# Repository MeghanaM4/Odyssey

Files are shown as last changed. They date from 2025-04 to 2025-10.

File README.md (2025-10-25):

# Odyssey

> a project for [apex.hackclub.com](https://apex.hackclub.com) by Meghana Madiraju and help from Kieran Klukas

I have been in love with space for as long as I can remember, so when I heard Hack Club was letting teenagers send whatever they want 113,000 feet in the air I knew I had to do it. We get $100 per person to make an invention that'll go onto a high altitude balloon (HAB), and if you spend 30 hours on it you'll get to go to Boston for a hackathon where everyone will launch their payloads at the same time and make cool stuff.

## Quick Overview (what we're sending up)
- Sensor data from SMD components on PCB (stored on a microSD card)
- PCB powered by 3 AA batteries that can survive -45C
- Internal camera that can see internal content
- 8 digit 7-segment display that show the current altitude, which the int. camera can also see

## Collected data
- Pressure
- Magnetic field (3-axis)
- Internal temperature of payload
- Gyroscopic data (3-axis)

## Component Stack
| Component | Purpose |
| --- | --- |
| Seeed Studio XIAO RP2040 | Main microcontroller |
| MS560702BA03-50 | Altimeter |
| MPU-6050 | Gyroscope/accelerometer |
| ALS31313KLEATR-1000 | Magnetometer |
| Mini Body Cam | Internal view of payload | 

View the complete BOM [here](https://docs.google.com/spreadsheets/d/1y77u3fouo9j1fYMRJqijLE8DN1v_GkXtAQhd4oCJCtc/edit?usp=sharing)          
<br>
## PCB
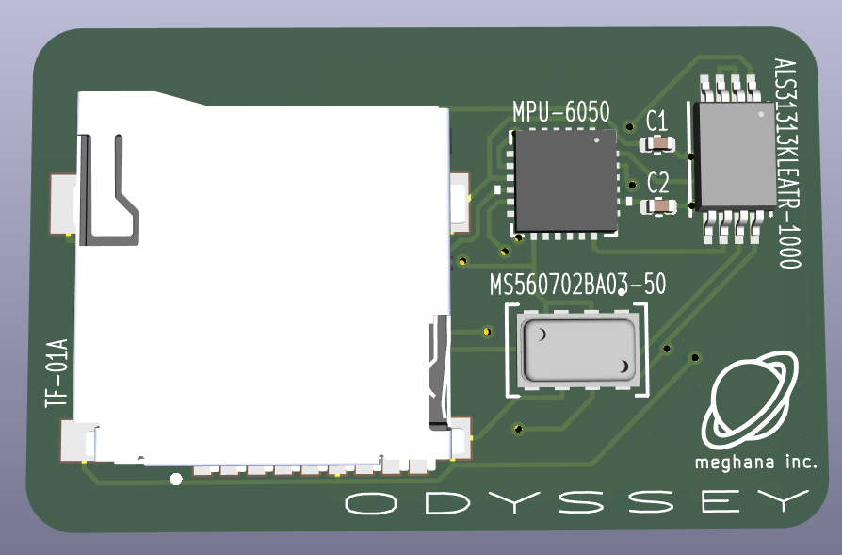
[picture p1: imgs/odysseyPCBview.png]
Odyssey PCB CAD rendering
             
<br>

## Timeline
| Phase | Status (%)|
| --- | --- |
| Research + Planning | 100% |
| Designing PCB and electronics layout | 100% | 
| Building payload | 100% |
| Coding firmware | 100% |
| Final tests and edits | 100% |
| Launch | 100% |

## Internal Camera View
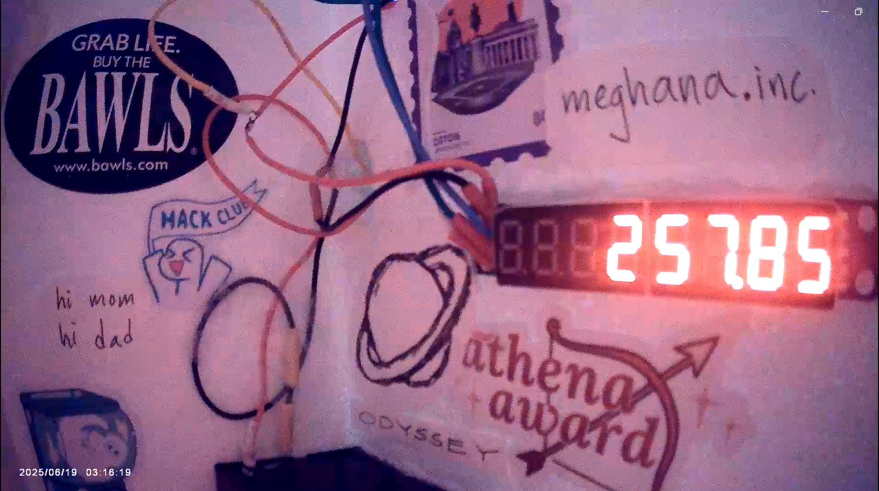
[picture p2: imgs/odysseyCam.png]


## External View


## Design Process
My first sketch of Odyssey looked like this:
<br>
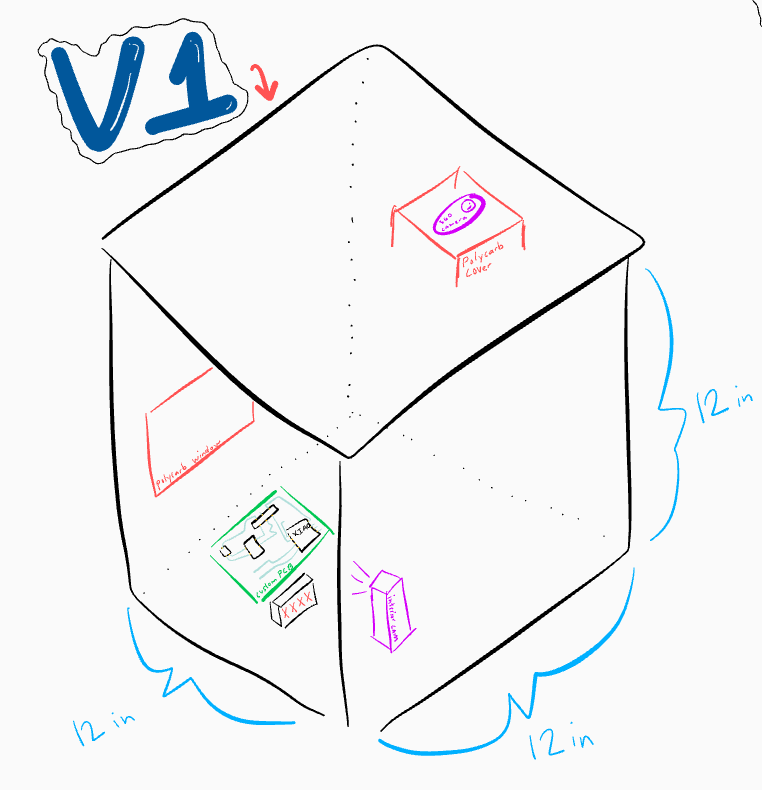
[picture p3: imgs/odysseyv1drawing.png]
Odyssey v1 drawing

<br>
The main PCB (the green square artfully drawn in the center, complete with blue copper traces) with the XIAO and SMDs would process and collect data. The 4 digit 7-segment display displays the altitude of the payload (math that would be calculated from the barometer), and would sit in front of an internal camera (the purple box) so the altitude could be captured in the video feed. The internal camera would also look outside via the polycarbonate window that I am going to steal from my robotics team's shop (sorry Mr. S).      
The camera on top was originally meant to capture the sky, but then I found out all the payloads would be aligned on top of eachother candy-necklace style, so I scrapped that pretty quick.

The second sketch had some improvements:
<br>
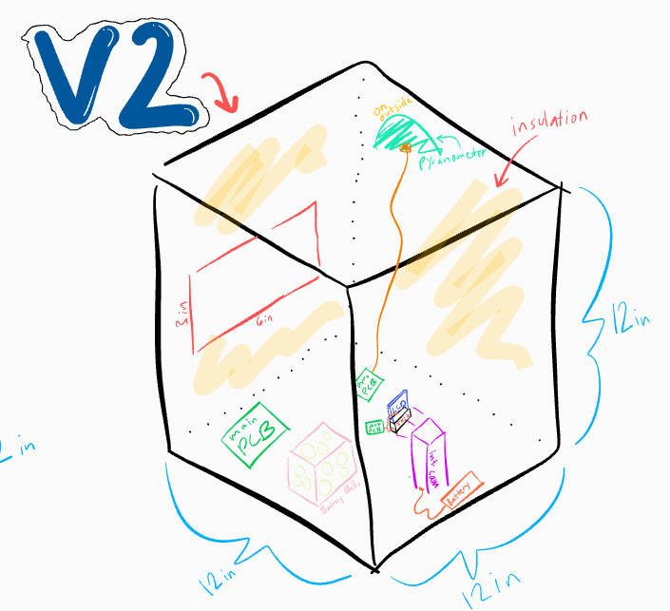
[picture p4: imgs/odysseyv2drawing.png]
Odyssey v2 drawing

<br>

I thought that we would need 3 PCBs: one for the main sensors, one for the LCD screen and 7-seg display, and one for the pyranometer. What's overkill? This obviously was taken out after I thought about a bit more (see: overkill) and after I saw the customs and duties taxes. The yellow stuff you see on the walls is my artistic interpretation of spray insulation.      

I really wanted our data to be space-focused, so getting a pyranometer to measure cosmic ray data was at the top of my list. Unfortunately, the Apogee Instrument component I found was a massive pain to work with, so I decided to just scrap it. If I get the basic functionality of everything else working, then I'll look into aurora borealis or radiation detection. The challenge is that those have to be on the outside of the payload, or at least shielded solely by polycarb or some other low-z window material.

I also drew a sketch of what I wanted the internal view to be:
<br>
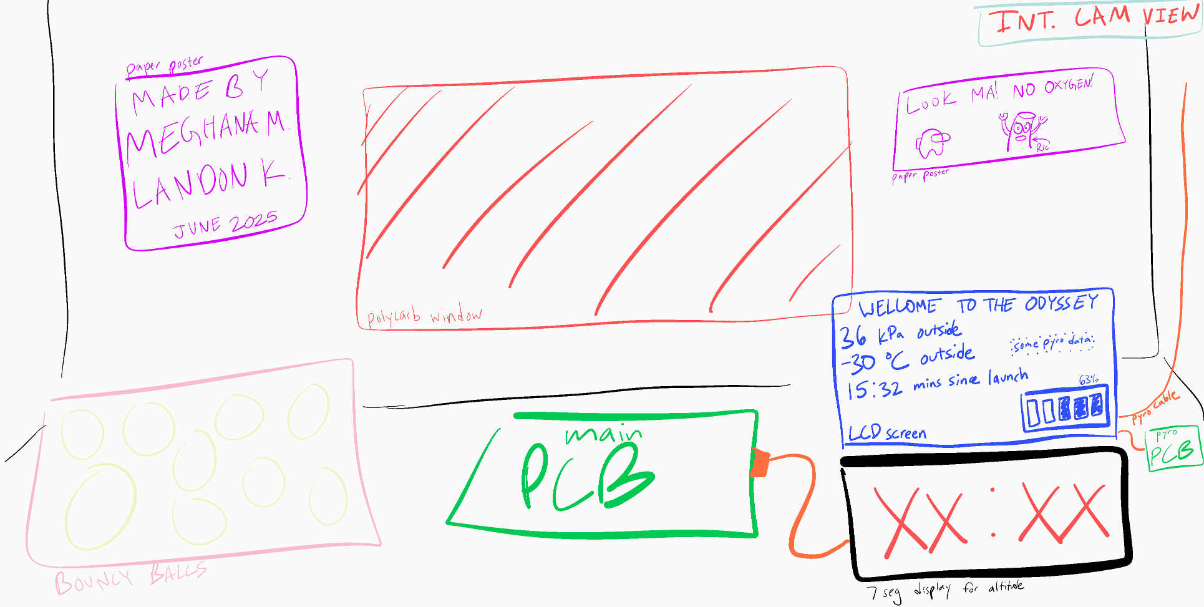
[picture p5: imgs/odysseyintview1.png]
Odyssey internal camera view v1

<br>

Here's an updated internal view with a smaller box and an updated layout:
<br>
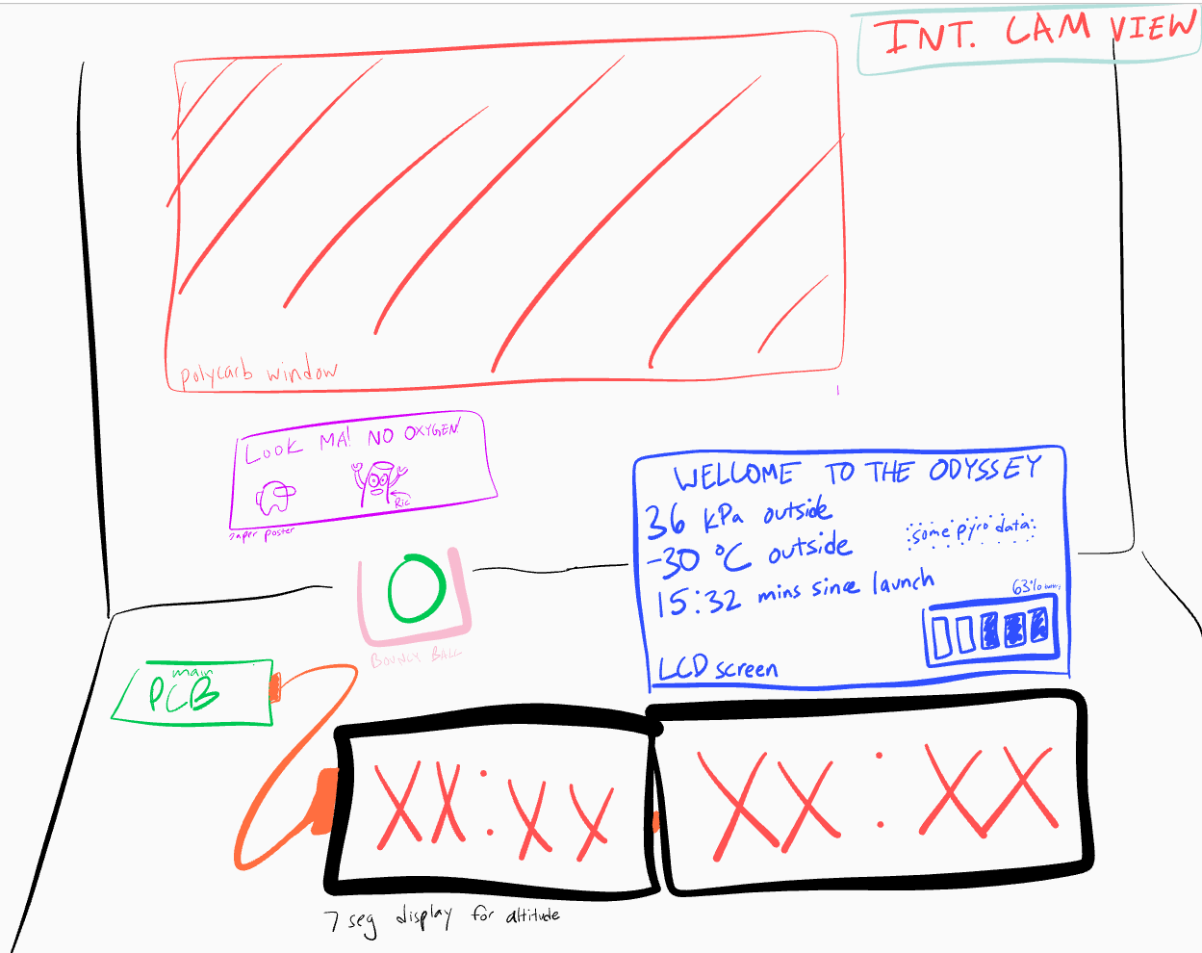
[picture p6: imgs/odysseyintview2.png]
Odyssey internal camera view v2

<br>

At this point, I planned for a PCB to store data from 3 sensors onto a microSD card, an internal camera that I charged to take a video of the entire flight, and 2 4-digit 7-segment displays to show the altitude as the payload rose. I hadn't yet figured out how to power the 7seg displays, or how I was going to control it (since the PCB didn't have enough open GPIO pins). I ordered 2 PCBAs of JLCPCB (I had to ship it to my friend in Canada, who then shipped it to me, to avoid the tariffs), Kieran and I soldered  the XIAO RP2040 on the back, and we started reading from the sensors.      
<br>
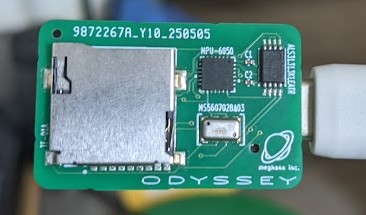
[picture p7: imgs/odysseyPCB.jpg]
Finished Odyssey PCB

<br>
I wanted the current altitude of the payload displayed on two 4-digit 7-segment displays so that the internal camera could see it, and realized quickly that I would need like 28 GPIO pins if I directly connected them both to a microcontroller, so that was a no go. I then found out that there's ICs that are made for controlling these kinds of things, so I spent the last of my $100 grant and got to work.

Bit of a change in plans. The MAX7219 driver chip I wanted to use to control the 7 segment displays didn't work and the libraries people used were like falling apart, so I was on the verge of severely rethinking plans. Then, Kieran came up with the wonderful idea of transmitting the altimeter data from the XIAO RP2040 (on the main PCB) to another microcontroller, so that we would have enough GPIO pins to directly wire the 7seg display.

Then, we remembered that we need two 4 digit 7seg displays, so we were like "let's send data from the xiao rp2040 to 2 other microcontrollers, one has the first 4 digits of the altitude and one has the last 4." Insane. So I'm working on that right now. We got connection between the xiao rp2040 and a xiao nrf52840 sense, but the sense doesn't have enough GPIO pins so Kieran kindly decided to lend me 2 orpheus picos (shout out Adam).
> An Orpheus Pico is a cheaper version of the raspberry pi pico made by @adammakesthingsdev that Hack Club used to make and distribute to people

I keep getting a transmission timing error between the xiao rp2040 and the pico, and I don't know how to fix it. Part of me thinks it's how I wired my pull up resistors (translating breadboard wiring to parallel and series diagrams in my head is rough), but I have no idea. At least I can flash code on the pico now, I dealt with a BOOTSEL issue for like 3 hours yesterday.

So after days of trying to get I2C to work, I decided to switch to SPI. And I kept getting errors there too. I think I've discovered my problem: because I'm using an orpheus pico but setting Arduino IDE's board to a raspberry pi pico, the default MOSI, MISO, and SCK (and therefore the SCL and SDA) pins don't match the orpheus pico's (because they have different internal stuff). So the problem was arduino the whole time. I knew that was gonna be an issue. Damn it. When I tried to set the SDA and SCL pins before Wire.begin() the pico used to crash and not execute any code, that's why I switched to SPI. this is crazy.

So, I'm spending more money. I've given up on communicating between the xiao rp2040 and another microcontroller. I'm going to buy an 8 digit 7seg display that has 5 pins that I can directly wire to my xiao rp2040. My only concern is that it uses the same MAX7219 driver chip that didn't work for me before (and whose library was also garbage), but other people got this thing to work and maybe those errors was me wiring wrong or doing something dumb. I've been trying for like a week to get this right and now I have to just pray to god that this New Method will work. This sucks balls.

The new display came, and after it (inevitably) didn't work, I resoldered the connections I had. Who knew that when your wires look like this some stuff is bound to break?

my god awful soldering job

Anyway, here's what it looked like after. 

my okay soldering job

> I made the mistake of getting 16 gauge wire. I spent ages at Lowe's trying to find like reasonable electrical wire but all of it was like Lamp Wire or Speaker Wire or Roof Tubing Heavy Duty Fracking Wire. Then, I tried to look for 24 gauge wire (thanks @Karmanyaah) but apparently none exists within a 50 mile radius of me so I had to buy it from amazon and get it shipped the next day. What you see above is me thinning out the ends of the wire so I can actually solder it. I've added an "idiot" column to my BOM.            

The display worked! Wow, the wonders of not being lazy.



But that was on the wrong microcontroller. I'd gotten it to work on the XIAO nRF52840 Sense that I had because, for some reason, it wouldn't work on my xiao RP2040. I dug out my dad's multimeter and found out it wasn't because of my soldering (win), but because of STUPID PIN ASSIGNMENTS. WHAT THE FREAK. On the xiao nRF you just put the GPIO assignment (D7 = 7), which is fine. But on the xiao rp2040 for some reason D10 is actually 3??? What?? Anyway, I got it work.



So with my camera set up (I had to buy another one since the first one was too cheap to work), the inside of the payload will look a bit like this. (the camera quality is better than this, I'm using a screenshot from a video of a video)



I've weighed the thing and I'm about 100g over (the whole thing is supposed to be 3/4 lbs or ~340 grams), so I'm planning to build the entire thing, be as wire-conscious as possible, and use my soldering iron to burn away any excess weight I might have after it's all done.
> Fun Fact: Burnt stryofoam fumes are carcinogenic!

I'm glad I'm not like insanely overweight because I hadn't weighed it up till now and was just kind of praying.

Yeah okay it's overweight. I didn't realize how much 100g of styrofoam actually was. It's like, a lot. I spent 10 minutes using my crappy $10 soldering iron to burn/melt away some of the sides of the box, and then I just started coughing a ton so I was like "that's probably a sign to stop" 

> did I mention styrofoam fumes are carcinogenic?

Anyway, I only got a gram off or something. 

Then, as I waited for my bedroom to stop becoming a Hazardous Zone, I went outside and started chopping away at the box with a massive serated kitchen knife. That only yielded about a gram, too. No dice.
> My window was open and the ceiling fan was running. My lungs feel okay.

Then I was just like "screw it" and destroyed my box to make a smaller one. An hour later, ta da! All that funky texture is my previous attempt at burning away material, and (as I'm sure you can guess) ruining my soldering iron in the process. It's strong, it'll push through.

I committed styrofoam murder to get to this point

Updated inside view (no wires): 

I committed styrofoam murder to get to this point

Tomorrow I'll glue the sides of the box together with gorilla glue and spray insulation/gap filler, and then I'll start soldering. We're so back.
> It's 2am.

So I sprayed insulation and gap filler and got everything pretty nice and laid out. I soldered the entire circuit and with some minor adjustments (I soldered the wrong pins of the rocker switch and I switched the 5V and GND junctions), it worked. My 7 segment display is showing altitude and everything is awesome.

hooray!

So then I stuck all its guts inside, taped some stuf down, and it now looks like this. Everything is awesome.

neat and tidy

So remember when I said everything is awesome? Turns out it's not. I'd run code for the 7 segment display and that worked, and I had code to log sensor data onto the microSD card, so I assumed everything would be fine when you put them together. Well was it? No, of course not. I was using SPI communication for both storing data on the microSD card and communicating with the 7 segment display. When I implemented the LedControl library in my log code, my display worked but it kept printed "Error opening file" to the serial monitor.

_Frick_ 

The display and SD card trying to communicate at the same time was screwing everything up, because signals it was sending overlapped with eachother and caused a bunch of nonsense. I immediately assumed that the problem couldn't be fixed, and that I'd have to sacrifice the display and it would all be sad. I'd tried to manually activate and deactivate the display by digitalWriting its chip select LOW and HIGH whenever the display was supposed to be silent, but it didn't work.
> Apparently, you're not supposed to do that.

Then, I thought that I should only update the display once every second, hoping that would slow down communication and the handling would be better. Also didn't work.

_Friiiiiiick_

Then, it hit me. I used the xiao's MISO pin for both components, not thinking about how that literally makes no sense. My serial clock was also connected to a pin that was already in use by the PCB, so that was an issue as well. I had 2 unconnected pins on my PCB. One I was using as my display's chip select (by complete chance) and one that I hadn't soldered to anything. I needed 3. DIN, CLK, and CS. I looked back at my KiCAD schematic and saw that I had interrupt pins for my magnetometer and my gyroscope, and realized I wasn't using them at all. 
> I was using polling, which is apparently way less efficient.

Since I wasn't using either of those pins, I soldered my DIN wire to my magnetometer interrupt pin and my CLK to the other unconnected GPIO I had. Still didn't work.

_Friiiiiiiiiiiiiiiiiiiiiiick_

Then I was like "what if the magnetometer is still using the interrupt pin, even though I'm not. It could be sending whatever it wants, or like bugging out and being random" (technical terms). So I cut its little ssop 8 legs off and tested it. 

It worked.

> Thank god, I was nearing the martian levels of self-inflicted disasters

Anyway, so everything's good now. Look at the inside!



I'm not doing a polycarb window anymore, partly because of time (my flight's tomorrow) and partly cause I'm scared to do anything else to this thing. I'm pretty happy with it.

----------------------
Update: I launched! Apex was an awesome event. After a nasty takeoff that made everyone's payloads hit the ground on takeoff, the balloons rose to about 100,000 feet in the air before popping. Unfortunately, the balloon my payload was on (there were 2) was the one that got stuck in a tree and was unrecoverable. So although I will never get to see what the camera saw, I can't believe I actually did it.

_This update was made about 4 months after Apex happened. I got a bit sidetracked (check out [Pathfinder](https://pathfinder.hackclub.com) and [Daydream](https://daydream.hackclub.com))_

## Big thank you to
-My teachers for putting up with my late work      
-My parents for letting me work on this instead of school       
-Kieran for answering all my questions

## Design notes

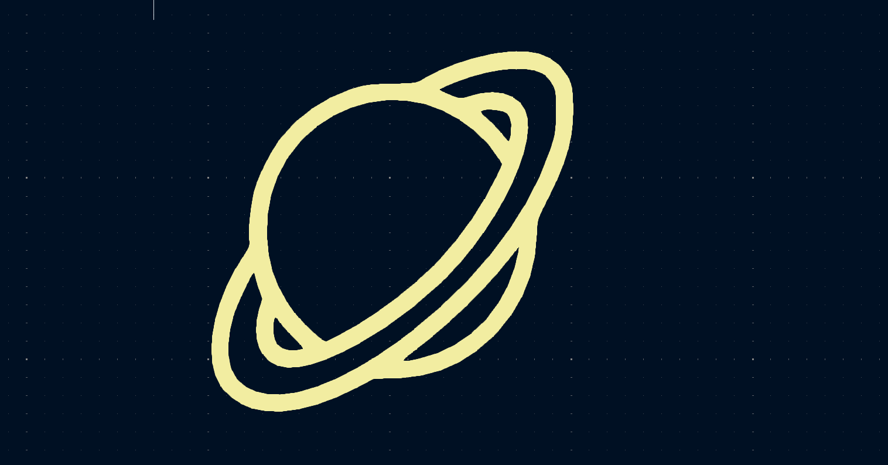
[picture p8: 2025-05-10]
kicad/madplanet.png

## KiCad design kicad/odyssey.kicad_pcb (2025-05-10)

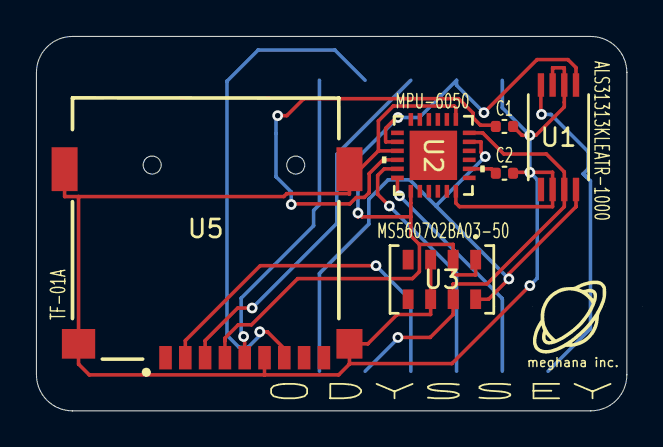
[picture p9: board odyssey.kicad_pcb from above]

Board: 2 copper layers, 32.8 x 20.8 mm, 7 parts (1 on the bottom side), 13 nets.

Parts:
C1, C2: C; C_0402_1005Metric
U1: ALS31313KLEATR-1000; TSSOP8_LE_ALM
U2: MPU-6050; QFN24_4X4X0P9-0P5_TDK
U3: MS560702BA03-50; SON8_MS5611_TEC
U4: XIAO-RP2040-SMD
U5: TF-01A

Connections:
3.3V: U1.1 (VCC), U2.8 (VLOGIC), U2.13 (VDD), U3.1 (VDD), U3.2 (PS), U4.12 (3V3), U5.4 (VDD)
GND: C1.1, C2.1, U1.2 (ADR0), U1.3 (GND), U1.6 (ADR1), U2.1 (CLKIN), U2.9 (AD0), U2.18 (GND), U3.3 (GND), U3.6 (SDO), U4.13 (GND), U5.6 (VSS), U5.MP1 (SHIELD), U5.MP2 (SHIELD), U5.MP3 (SHIELD), U5.MP4 (SHIELD)
GYROFSYNC: U2.11 (FSYNC), U4.3 (GPIO28_A2_D2)
GYROINT: U2.12 (INT), U4.2 (GPIO27_A1_D1)
MAGINT: U1.4 (*INT), U4.1 (GPIO26_A0_D0)
MSDCD: U4.4 (GPIO29_A3_D3), U5.2 (CD/DAT3)
MSDCLK: U4.9 (GPIO2_D8_SCK), U5.5 (CLK)
MSDMISO: U4.10 (GPIO4_D9_MISO), U5.7 (DAT0)
MSDMOSI: U4.11 (GPIO3_D10_MOSI), U5.3 (CMD)
unnamed: C2.2, U2.20 (CPOUT)
unnamed: C1.2, U2.10 (REGOUT)
SCL: U1.8 (SCL), U2.23 (SCL), U3.8 (SCLK), U4.6 (GPIO7_D5_SCL)
SDA: U1.7 (SDA), U2.24 (SDA), U3.7 (SDI/SDA), U4.5 (GPIO6_D4_SDA)

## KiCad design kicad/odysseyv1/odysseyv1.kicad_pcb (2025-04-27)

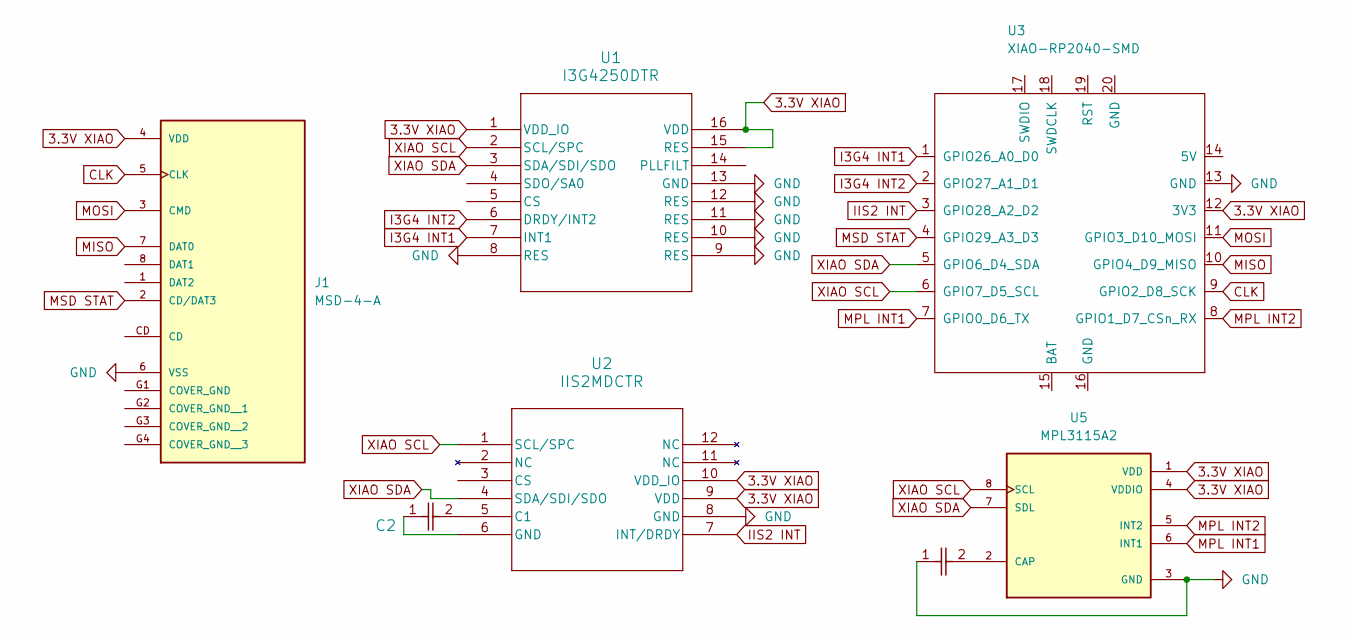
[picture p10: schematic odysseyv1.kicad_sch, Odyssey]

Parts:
C1: 0402B104K160CT; CAP_0402_N_WAL
C3: C2; CAP_0402_N_WAL
J1: MSD-4-A; CUI_MSD-4-A; PARTREV 1.0
U1: I3G4250DTR
U2: IIS2MDCTR
U3: XIAO-RP2040-SMD
U5: MPL3115A2; NXP_LGA-8_3x5mm_P1.25mm_H1.1mm

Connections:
3.3V XIAO: J1.4 (VDD), U1.1 (VDD_IO), U1.15 (RES), U1.16 (VDD), U2.9 (VDD), U2.10 (VDD_IO), U3.12 (3V3), U5.1 (VDD), U5.4 (VDDIO)
CLK: J1.5 (CLK), U3.9 (GPIO2_D8_SCK)
GND: C1.1, J1.6 (VSS), U1.8 (RES), U1.9 (RES), U1.10 (RES), U1.11 (RES), U1.12 (RES), U1.13 (GND), U2.8 (GND), U3.13 (GND), U5.3 (GND)
I3G4 INT1: U1.7 (INT1), U3.1 (GPIO26_A0_D0)
I3G4 INT2: U1.6 (DRDY/INT2), U3.2 (GPIO27_A1_D1)
IIS2 INT: U2.7 (INT/DRDY), U3.3 (GPIO28_A2_D2)
MISO: J1.7 (DAT0), U3.10 (GPIO4_D9_MISO)
MOSI: J1.3 (CMD), U3.11 (GPIO3_D10_MOSI)
MPL INT1: U3.7 (GPIO0_D6_TX), U5.6 (INT1)
MPL INT2: U3.8 (GPIO1_D7_CSn_RX), U5.5 (INT2)
MSD STAT: J1.2 (CD/DAT3), U3.4 (GPIO29_A3_D3)
unnamed: C3.1, U2.6 (GND)
unnamed: C3.2, U2.5 (C1)
unnamed: C1.2, U5.2 (CAP)
XIAO SCL: U1.2 (SCL/SPC), U2.1 (SCL/SPC), U3.6 (GPIO7_D5_SCL), U5.8 (SCL)
XIAO SDA: U1.3 (SDA/SDI/SDO), U2.4 (SDA/SDI/SDO), U3.5 (GPIO6_D4_SDA), U5.7 (SDL)

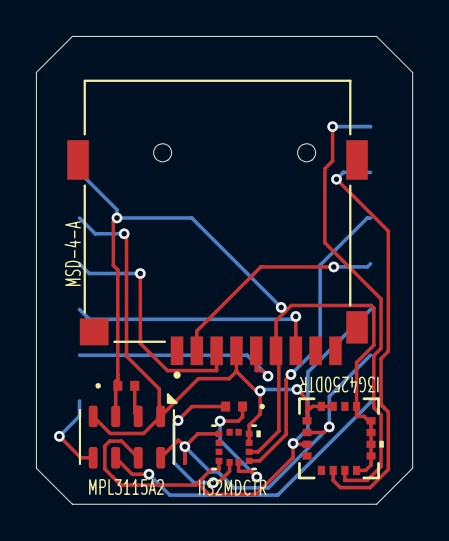
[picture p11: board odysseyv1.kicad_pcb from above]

Board: 2 copper layers, 20.9 x 26.0 mm, 7 parts (1 on the bottom side), 16 nets.

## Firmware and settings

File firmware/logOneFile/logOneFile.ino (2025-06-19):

#include <Wire.h>
#include <SPI.h>
#include <SD.h>
#include <LedControl.h>

//microSD card
const int chipSelect = 29;

const int displayDIN = 26;  //D0
const int displayCLK = 0;   //D6  
const int displayCS = 1;    //D7

//for time
long startTime = 0;

//MS5607 altimeter
#define MS5607_ADDR 0x77
#define CMD_RESET 0x1E
#define CMD_CONVERT_D1_4096 0x48
#define CMD_CONVERT_D2_4096 0x58
#define CMD_ADC_READ 0x00
#define CMD_PROM_READ 0xA0
uint16_t C[8];

//MPU6050 gyro
#define MPU6050_ADDR 0x68
#define MPU6050_PWR_MGMT_1 0x6B
#define MPU6050_ACCEL_XOUT_H 0x3B
#define MPU6050_GYRO_XOUT_H 0x43
#define MPU6050_TEMP_OUT_H 0x41

//ALS31313 hall effect
#define ALS31313_ADDR 0x60
#define ALS31313_X_LSB 0x28
#define ALS31313_X_MSB 0x29
#define ALS31313_Y_LSB 0x2A
#define ALS31313_Y_MSB 0x2B
#define ALS31313_Z_LSB 0x2C
#define ALS31313_Z_MSB 0x2D

LedControl lc = LedControl(displayDIN, displayCLK, displayCS, 1);

float temperature = 0, pressure = 0, altitude = 0;
float accelX = 0, accelY = 0, accelZ = 0;
float gyroX = 0, gyroY = 0, gyroZ = 0;
float magX = 0, magY = 0, magZ = 0, magMagnitude = 0;

bool start = true;
unsigned long lastUpdate = 0;

void setup() {
  Serial.begin(115200);
  
  SPI.begin();
  
  if (!SD.begin(chipSelect)) {
    Serial.println("SD card initialization failed");
    return;
  }
  Serial.println("SD card initialized.");

  Wire.begin();

  initMS5607();
  initMPU6050();
  initALS31313();

  lc.shutdown(0, false);
  lc.setIntensity(0, 1);
  lc.clearDisplay(0);

  delay(2000);
  startTime = millis();
}

void loop() {
  readMS5607();
  readMPU6050();
  readALS31313();

  logDataToSD();

  if (millis() - lastUpdate >= 200) { //to avoid overload
    displayNum(altitude);
    lastUpdate = millis();
  }

  delay(100);
}

void logDataToSD() {
  File datalog = SD.open("datalog.csv", FILE_WRITE);

  if (datalog) {
    if (start) {
      File errorlog = SD.open("errorlog.csv", FILE_WRITE);
      errorlog.println("Error log:");
      errorlog.close();
      datalog.println("Time (ms), Temp (C), Pressure (Pa), Altitude (m), Ax, Ay, Az, Gx, Gy, Gz, Mx, My, Mz, Mag");
      start = false;
    }

    datalog.print(millis() - startTime);
    datalog.print(", ");
    datalog.print(temperature);
    datalog.print(", ");
    datalog.print(pressure);
    datalog.print(", ");
    datalog.print(altitude);
    datalog.print(", ");
    datalog.print(accelX);
    datalog.print(", ");
    datalog.print(accelY);
    datalog.print(", ");
    datalog.print(accelZ);
    datalog.print(", ");
    datalog.print(gyroX);
    datalog.print(", ");
    datalog.print(gyroY);
    datalog.print(", ");
    datalog.print(gyroZ);
    datalog.print(", ");
    datalog.print(magX);
    datalog.print(", ");
    datalog.print(magY);
    datalog.print(", ");
    datalog.print(magZ);
    datalog.print(", ");
    datalog.println(magMagnitude);
    datalog.close();
  } else {
    File errorlog = SD.open("errorlog.csv", FILE_WRITE);
    if (errorlog) {
      errorlog.print("Error opening datalog file at ");
      errorlog.println(millis() - startTime);
      errorlog.close();
    }
    Serial.println("Error opening datalog file");
  }
}

bool initMS5607() {
  Wire.beginTransmission(MS5607_ADDR);
  Wire.write(CMD_RESET);
  if (Wire.endTransmission() != 0) return false;
  delay(10);

  for (int i = 0; i < 8; i++) {
    Wire.beginTransmission(MS5607_ADDR);
    Wire.write(CMD_PROM_READ + (i * 2));
    Wire.endTransmission();

    Wire.requestFrom(MS5607_ADDR, 2);
    if (Wire.available() >= 2) {
      C[i] = (Wire.read() << 8) | Wire.read();
    } else {
      return false;
    }
  }
  return true;
}

void readMS5607() {
  uint32_t rawPressure = readRawPressure();
  uint32_t rawTemp = readRawTemperature();

  int32_t dT = rawTemp - ((uint32_t)C[5] << 8);
  int32_t TEMP = 2000 + (((int64_t)dT * C[6]) >> 23);

  int64_t OFF = ((int64_t)C[2] << 17) + (((int64_t)C[4] * dT) >> 6);
  int64_t SENS = ((int64_t)C[1] << 16) + (((int64_t)C[3] * dT) >> 7);

  int32_t P = (((rawPressure * SENS) >> 21) - OFF) >> 15;

  temperature = TEMP / 100.0;
  pressure = P / 100.0;
  altitude = 44330.0 * (1.0 - pow(pressure / 1013.25, 0.1903));
}

uint32_t readRawPressure() {
  Wire.beginTransmission(MS5607_ADDR);
  Wire.write(CMD_CONVERT_D1_4096);
  Wire.endTransmission();
  delay(10);

  Wire.beginTransmission(MS5607_ADDR);
  Wire.write(CMD_ADC_READ);
  Wire.endTransmission();

  Wire.requestFrom(MS5607_ADDR, 3);
  uint32_t result = 0;
  if (Wire.available() >= 3) {
    result = ((uint32_t)Wire.read() << 16) | ((uint32_t)Wire.read() << 8) | Wire.read();
  }
  return result;
}

uint32_t readRawTemperature() {
  Wire.beginTransmission(MS5607_ADDR);
  Wire.write(CMD_CONVERT_D2_4096);
  Wire.endTransmission();
  delay(10);

  Wire.beginTransmission(MS5607_ADDR);
  Wire.write(CMD_ADC_READ);
  Wire.endTransmission();

  Wire.requestFrom(MS5607_ADDR, 3);
  uint32_t result = 0;
  if (Wire.available() >= 3) {
    result = ((uint32_t)Wire.read() << 16) | ((uint32_t)Wire.read() << 8) | Wire.read();
  }
  return result;
}

bool initMPU6050() {
  Wire.beginTransmission(MPU6050_ADDR);
  if (Wire.endTransmission() != 0) return false;

  Wire.beginTransmission(MPU6050_ADDR);
  Wire.write(MPU6050_PWR_MGMT_1);
  Wire.write(0);
  return (Wire.endTransmission() == 0);
}

void readMPU6050() {
  Wire.beginTransmission(MPU6050_ADDR);
  Wire.write(MPU6050_ACCEL_XOUT_H);
  Wire.endTransmission(false);
  Wire.requestFrom(MPU6050_ADDR, 14, true);

  if (Wire.available() >= 14) {
    int16_t axRaw = Wire.read() << 8 | Wire.read();
    int16_t ayRaw = Wire.read() << 8 | Wire.read();
    int16_t azRaw = Wire.read() << 8 | Wire.read();

    Wire.read();
    Wire.read();  //Skip temperature readings

    int16_t gxRaw = Wire.read() << 8 | Wire.read();
    int16_t gyRaw = Wire.read() << 8 | Wire.read();
    int16_t gzRaw = Wire.read() << 8 | Wire.read();

    accelX = axRaw / 16384.0;
    accelY = ayRaw / 16384.0;
    accelZ = azRaw / 16384.0;

    gyroX = gxRaw / 131.0;
    gyroY = gyRaw / 131.0;
    gyroZ = gzRaw / 131.0;
  }
}

bool initALS31313() {
  Wire.beginTransmission(ALS31313_ADDR);
  return (Wire.endTransmission() == 0);
}

void readALS31313() {
  int16_t magXRaw = readALS31313Register(ALS31313_X_MSB, ALS31313_X_LSB);
  int16_t magYRaw = readALS31313Register(ALS31313_Y_MSB, ALS31313_Y_LSB);
  int16_t magZRaw = readALS31313Register(ALS31313_Z_MSB, ALS31313_Z_LSB);

  magX = magXRaw * 0.0001;
  magY = magYRaw * 0.0001;
  magZ = magZRaw * 0.0001;

  magMagnitude = sqrt(magX * magX + magY * magY + magZ * magZ);
}

int16_t readALS31313Register(uint8_t regMSB, uint8_t regLSB) {
  uint8_t msb = 0, lsb = 0;

  Wire.beginTransmission(ALS31313_ADDR);
  Wire.write(regMSB);
  Wire.endTransmission();
  Wire.requestFrom(ALS31313_ADDR, 1);
  if (Wire.available()) msb = Wire.read();

  Wire.beginTransmission(ALS31313_ADDR);
  Wire.write(regLSB);
  Wire.endTransmission();
  Wire.requestFrom(ALS31313_ADDR, 1);
  if (Wire.available()) lsb = Wire.read();

  return (int16_t)((msb << 8) | lsb);
}

void displayNum(float num) {
  char buffer[10];
  sprintf(buffer, "%8.2f", num);

  int digit = 0;

  for (int i = 7; i >= 0; i--) {
    if (buffer[i] == '.') {
      if (i > 0 && buffer[i - 1] != ' ') {
        lc.setChar(0, digit, buffer[i - 1], true);
        i--;
      }
    } else if (buffer[i] != ' ') {
      lc.setChar(0, digit, buffer[i], false);
    } else {
      lc.setChar(0, digit, ' ', false);
    }
    digit++;
  }
}

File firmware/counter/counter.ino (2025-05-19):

/*
    A
   ---
F |   | B
  | G |
   ---
E |   | C
  |   |
   ---
    D
  This example code is in the public domain.
 */
 
// Note: this organization sucks and make it better

int pinA = 6;
int pinB = 7;
int pinC  = 8;
int pinD = 9;
int pinE = 10;
int pinF = 12;
int pinG = 11;
int Dig1 = 2;
int Dig2 = 3;
int Dig3 = 4;
int Dig4 = 5;
int DP = 13;

int pins[] = {Dig1, Dig2, Dig3, Dig4, pinA, pinB, pinC, pinD, pinE, pinF, pinG, DP};
int segPins[] = {pinA, pinB, pinC, pinD, pinE, pinF, pinG};
int digPins[] = {Dig1, Dig2, Dig3, Dig4};

const uint8_t numPatterns[10] = {
  0x3F, // 0 => segments a,b,c,d,e,f
  0x06, // 1 => segments b,c
  0x5B, // 2 => a,b,d,e,g
  0x4F, // 3 => a,b,c,d,g
  0x66, // 4 => b,c,f,g
  0x6D, // 5 => a,c,d,f,g
  0x7D, // 6 => a,c,d,e,f,g
  0x07, // 7 => a,b,c
  0x7F, // 8 => a,b,c,d,e,f,g
  0x6F  // 9 => a,b,c,d,f,g
};

int pow10[] = {1, 10, 100, 1000};

void setup() {     

  for(int pin : pins) {
    pinMode(pin, OUTPUT);
  }

  turnOffSegs();
  turnOffDigs();
}

void loop() {
  for (int i = 0; i < 2048; i++) {
    unsigned long tStart = millis();
    while (millis() - tStart < 200) {
      refreshDisplay(i); // keep showing the number for 200ms
    }
  }
}


void turnOffDigs() {
  for(int pin : digPins) {
    digitalWrite(pin, HIGH);
  }
}

void turnOffSegs() {
  for(int pin : segPins) {
    digitalWrite(pin, LOW);
  }
}

void setSegs(uint8_t pattern) {
  for (int i = 0; i < 7; i++) {
    bool segmentOn = pattern & (1 << i);
    digitalWrite(segPins[i], segmentOn ? HIGH : LOW);
  }
}

void displayDigit(int digit, int position) {
  if (digit < 0 || digit > 9 || position < 0 || position > 3) return;
  turnOffDigs();
  setSegs(numPatterns[digit]);
  digitalWrite(digPins[position], LOW); // Enable digit (common cathode)
  delay(5);
  digitalWrite(digPins[position], HIGH); // Disable digit after delay
}

void displayNum(int number) {
  if (number < 0) number = -number;
  if (number > 9999) number = 9999;

  for (int i = 3; i >= 0; i--) {
    int digit = number % 10;   
    displayDigit(digit, i);        
    number /= 10;
  }
}

void refreshDisplay(int number) {
  for (int pos = 0; pos < 4; pos++) {
    int digit = (number / pow10[3 - pos]) % 10;

    turnOffDigs();
    setSegs(numPatterns[digit]);
    digitalWrite(digPins[pos], LOW);

    delayMicroseconds(1000);
  }
}

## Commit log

2025-04-26 main pcb upload and pcb folders
    [CAP_0402_N_WAL.step, LGA-12_2X2X0P7_STM.step, LGA-16_4X4X1_STM.step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]
2025-04-27 updating main pcb
    [odyssey.kicad_pcb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]
2025-04-27 chore: move to standard kicad layout
    [odyssey.kicad_pcb, odyssey.kicad_sch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]
2025-04-27 feat: shrink board and autoroute
    [odyssey.kicad_pcb, odyssey.kicad_sch]
2025-04-29 updating pcb
    [odyssey.kicad_pcb, odyssey.kicad_sch, odysseyv1.kicad_pcb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]
2025-05-10 trying firmware stuff
    [odyssey.kicad_pcb, odyssey.kicad_sch]
2025-05-12 PCB picture
2025-05-12 pcb image
2025-06-03 primitive sensor reading tests
2025-06-03 plotting and logging sensor data !!
2025-10-25 Modify camera description in README
    Updated README to reflect changes in camera description.
